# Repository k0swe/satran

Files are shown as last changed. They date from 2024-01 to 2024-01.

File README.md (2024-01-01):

# Open source Azimuth/Elevation satellite antenna rotator for radio amateurs

- Designed by Daniel Nikolajsen, SM7YSA

The onboard microprocessor has wifi-capability and can be controlled
automatically with an easy to use android app that you can install for free from
Google Play, or with the free PC program Gpredict or other rotctld-compatible
software.

The rotator has a mount on top that allows for many different kinds of antennas,
perfect for getting started with satellite communications.

The MK3 Satellite Rotator is fully open source, allowing you to 3D-print the
parts at home for free and solder the PCBs by hand. Enjoy!

If you invent upgrades or find new ways of using the SATRAN, we hope that you
[contact us](https://www.satran.io/support/) and share your designs so we can
post it here on the website for all to enjoy.

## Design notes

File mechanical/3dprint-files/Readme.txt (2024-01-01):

/***********************************************
 2022-11-15
 SATRAN AZ/EL ROTATOR MK3 print files
 ---
 Design SM7YSA Daniel Nikolajsen <satran@danaco.se>
 Creative commons BY-NC-SA 2.0
 www.satran.io
***********************************************/

Gears recommended print settings
---
ASA, ABS or Nylon
0.4mm nozzle
0.15mm layer height
60-70% infill
30-40mm/s print speed
Gears should have a tight fit on to the motor or sensor axle. 
To increase/decrease play, adjust the
infill by 5-10% or resize the entire part by a few percent.

Housing recommended print settings
---
PLA or PETG
0.4mm nozzle
0.2mm layer height
50-60% infill
40-60mm/s print speed
Good luck!

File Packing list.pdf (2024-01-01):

## SATRAN MK3 Rotator – Bill of Materials

2022-09-02

1pcs Controller in plastic casing | 1pcs Rubber grommet PG16
1pcs Power cable | 4pcs Bolt M3x6mm
2pcs DC geared motor 60rpm | 9pcs Countersunk screw 3x10mm
1pcs Bearing 6806 | 14pcs Flange screw 3x8mm
1pcs Bearing F685 | 4pcs Bolt M3x12mm
2pcs Bearing 608 | 4pcs Lock nut M3
1pcs Control patch cable RJ45 | 5pcs Flange nut M8
1pcs Aluminum motor bracket | 2pcs Tapping screw 2.2x10mm
1pcs Aluminum antenna bracket | 7pcs Tapping screw 2.2x6.5mm
1pcs M8 axle with glued lock nut | 7pcs Bolt M5x16mm
1pcs 12volt power adapter | 3pcs Hex nut M5
1pcs 1-turn potentiometer 1kohm | 4pcs Lock nut M5

1pcs 10-turn potentiometer 1kohm

## 3D-printable parts

Official downloads available at www.satran.io/downloads

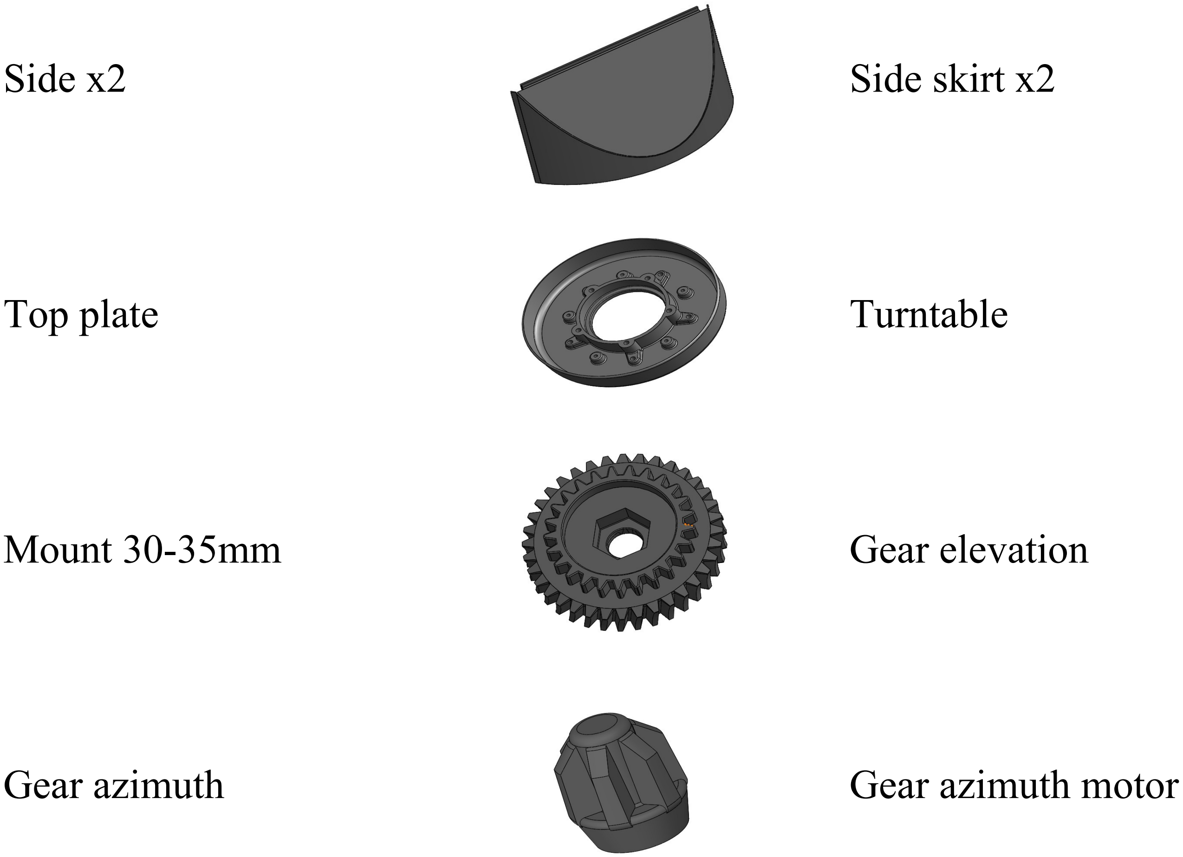
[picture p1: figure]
Side x2; Side skirt x2; Top plate; Turntable; Mount 30-35mm; Gear elevation; Gear azimuth; Gear azimuth motor
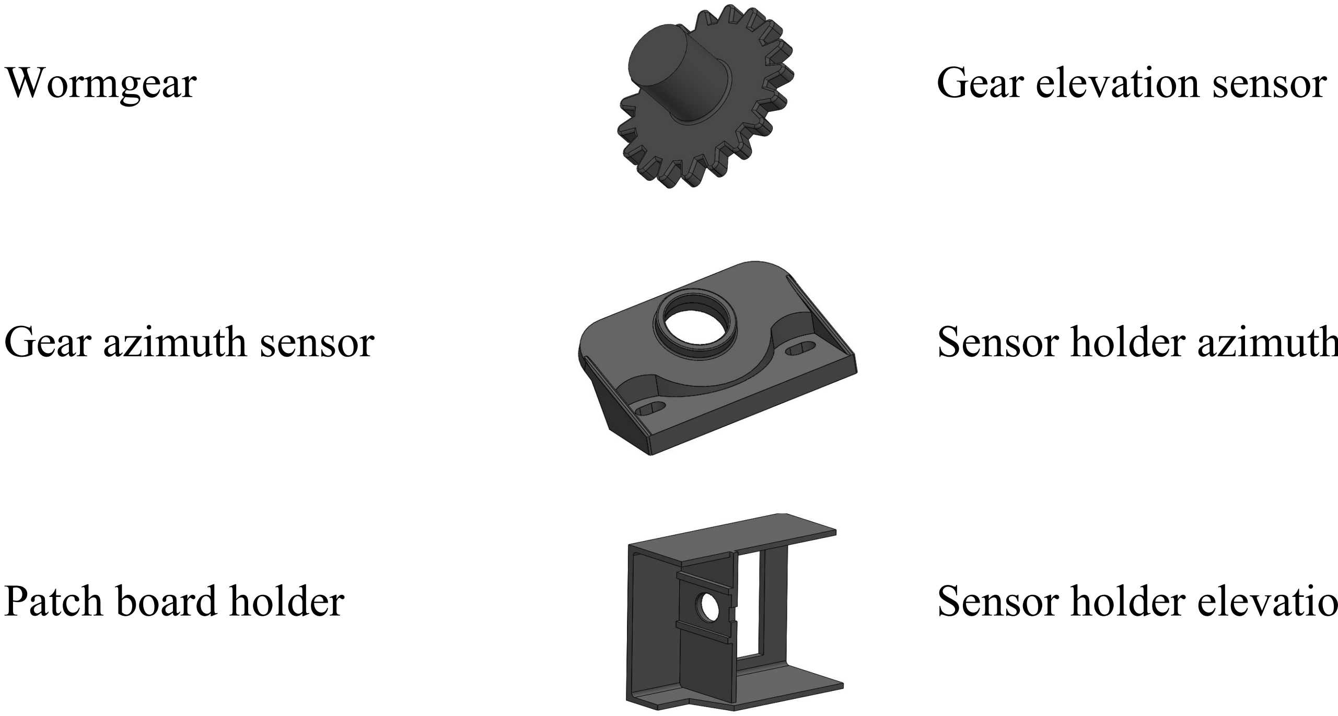
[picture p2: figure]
Wormgear; Gear elevation sensor

Gear azimuth sensor | Sensor holder azimuth

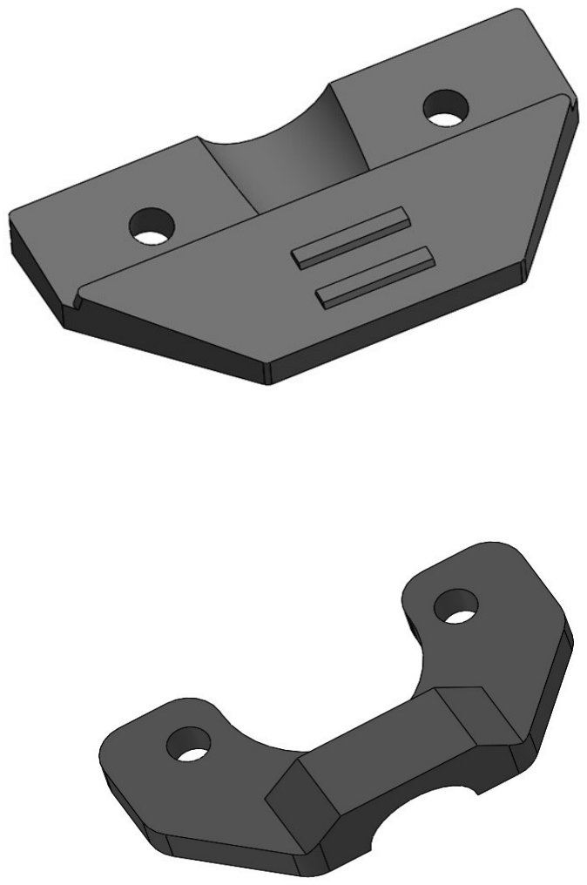
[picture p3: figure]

Patch board holder | Sensor holder elevation
Patch board clamp | Axle spacer

15/20mm antenna fastener

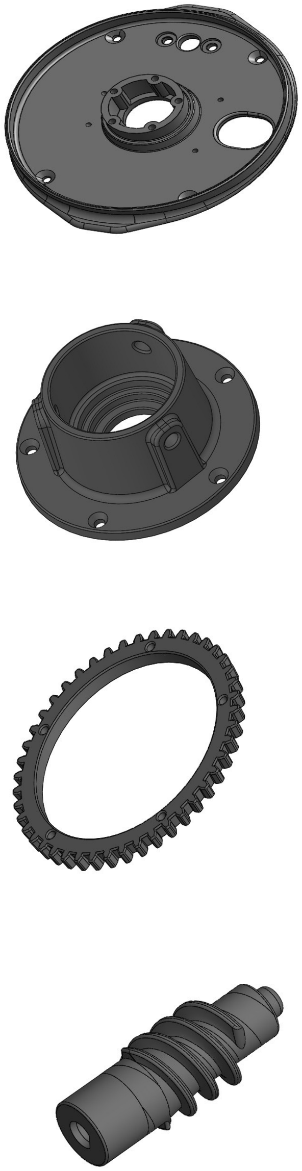
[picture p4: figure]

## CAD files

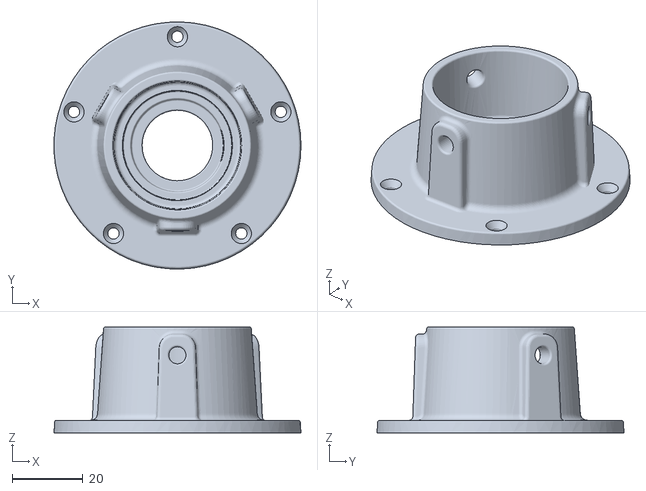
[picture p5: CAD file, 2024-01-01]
mechanical/3dprint-files/pipe-mount.STL
70.0 x 70.0 x 30.0

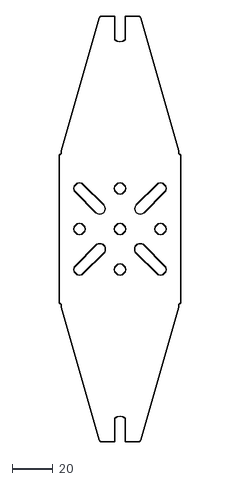
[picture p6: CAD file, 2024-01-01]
mechanical/Antenna bracket flat.dxf
60.0 x 210.0

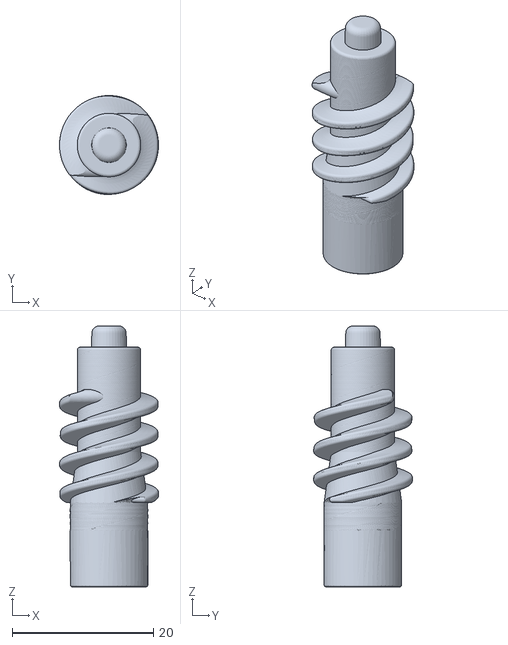
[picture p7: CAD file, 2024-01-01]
mechanical/3dprint-files/elevation-wormgear.STL
14.0 x 14.0 x 37.0

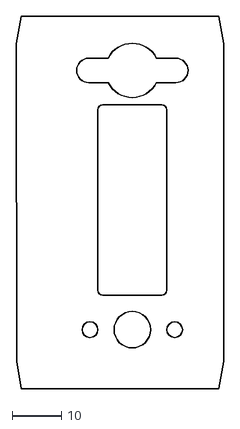
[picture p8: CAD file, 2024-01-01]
mechanical/Elevation motor bracket flat.dxf
42.0 x 75.6

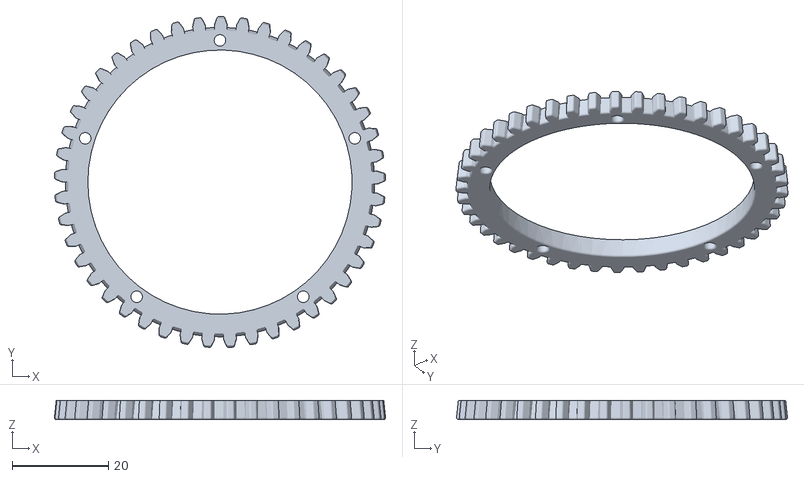
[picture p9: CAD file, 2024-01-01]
mechanical/3dprint-files/azimuth-stationary-gear.STL
68.9 x 68.9 x 4.00

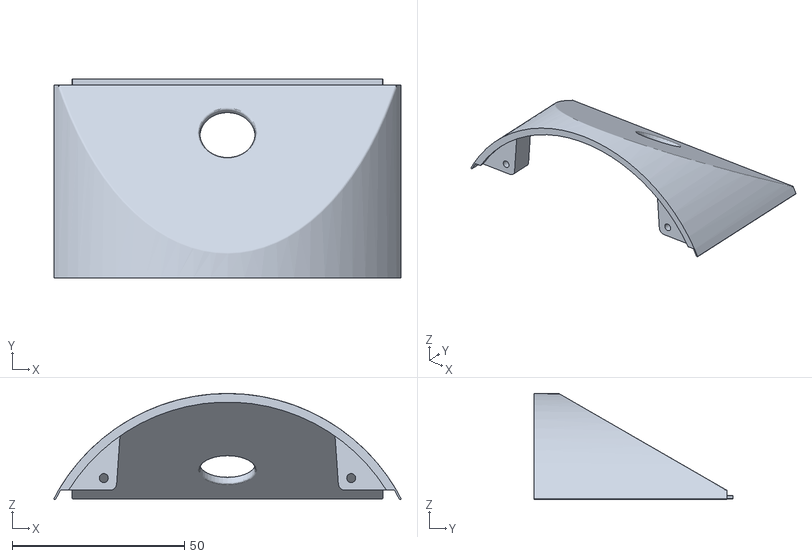
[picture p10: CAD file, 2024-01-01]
mechanical/3dprint-files/side-skirt-grommet.STL
100.8 x 57.8 x 30.8

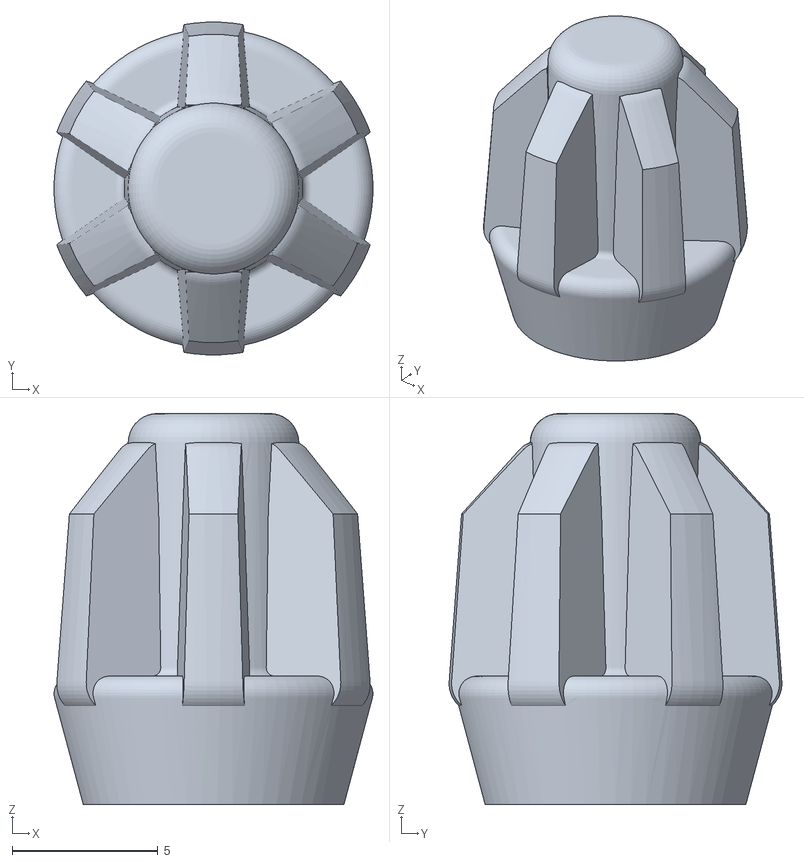
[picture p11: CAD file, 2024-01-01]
mechanical/3dprint-files/azimuth-motor-gear.STL
10.9 x 11.4 x 13.4

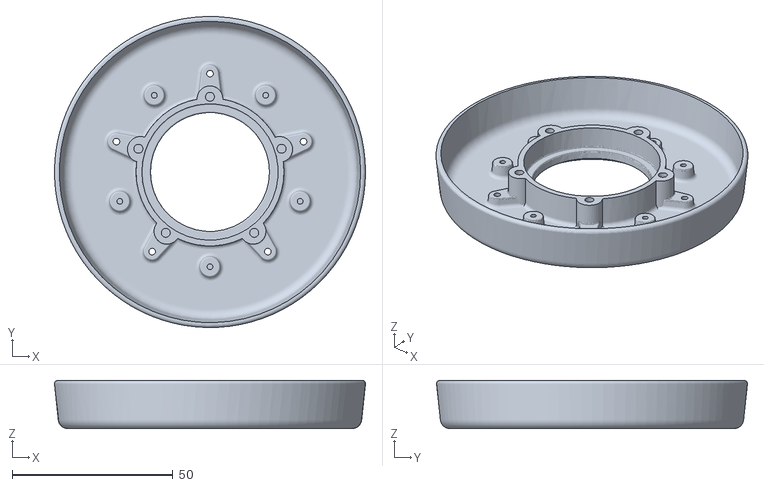
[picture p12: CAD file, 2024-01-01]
mechanical/3dprint-files/turntable.STL
96.8 x 96.8 x 15.0

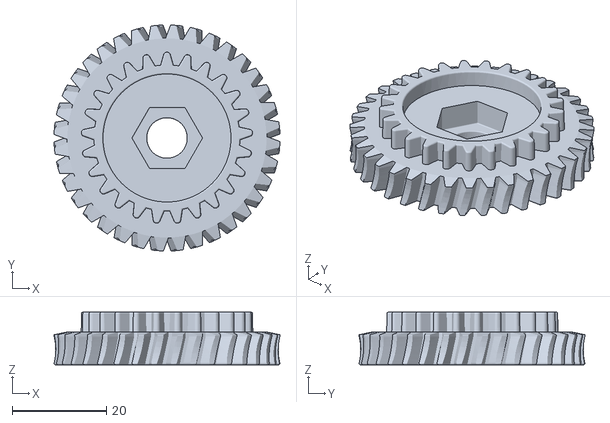
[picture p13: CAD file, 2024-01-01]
mechanical/3dprint-files/elevation-axle-gear.STL
48.0 x 48.0 x 11.2

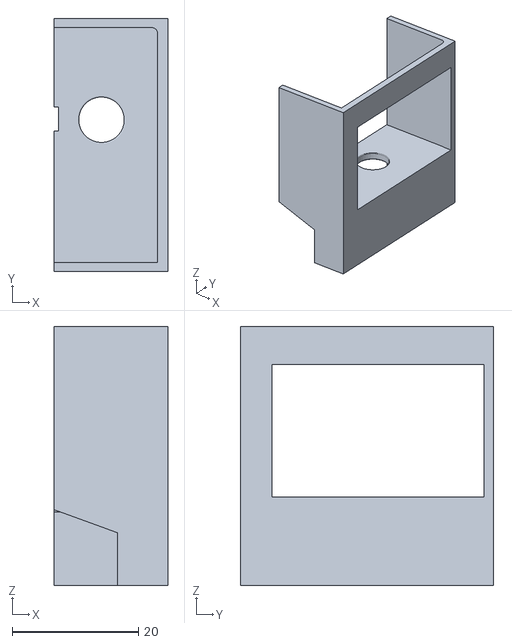
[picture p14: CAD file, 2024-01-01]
mechanical/3dprint-files/elevation-sensor-bracket.STL
18.0 x 40.0 x 41.0

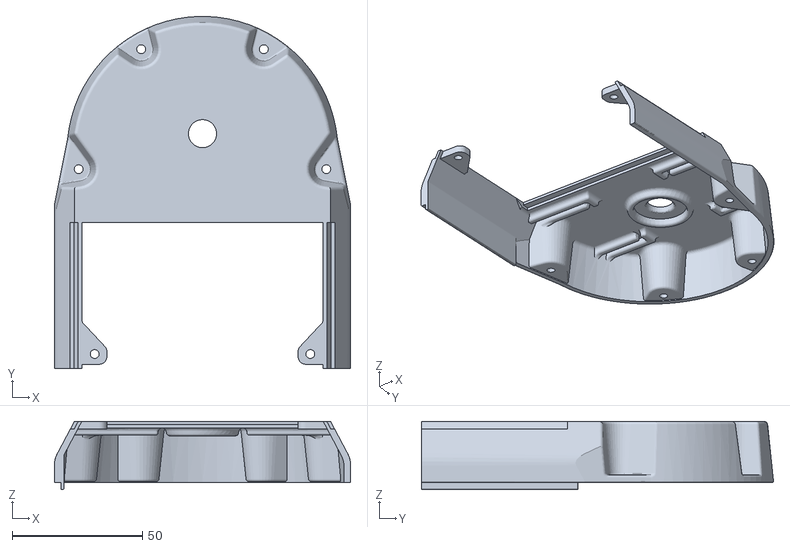
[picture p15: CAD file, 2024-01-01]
mechanical/3dprint-files/side-housing.STL
113.6 x 134.9 x 26.1

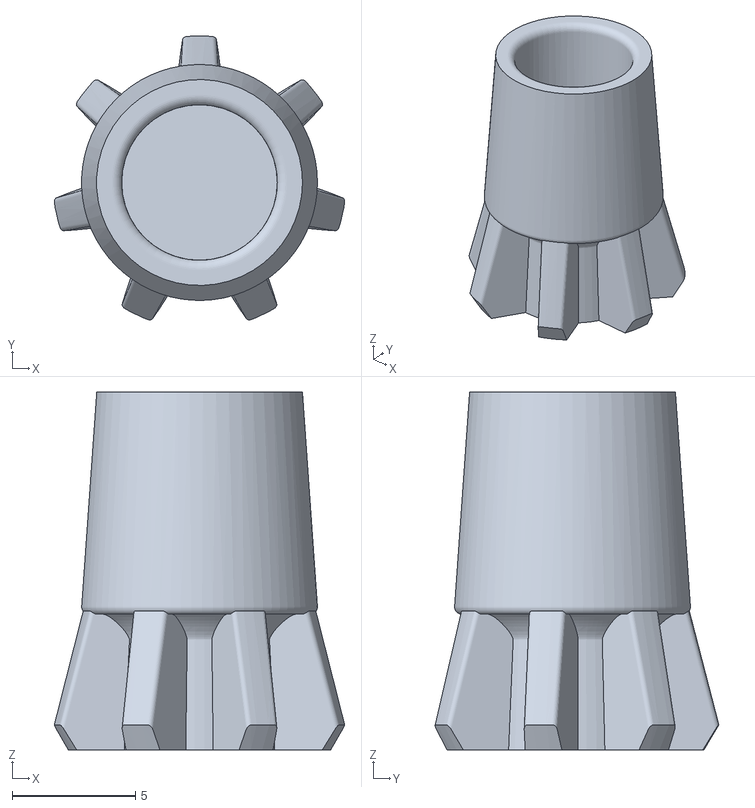
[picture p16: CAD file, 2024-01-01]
mechanical/3dprint-files/azimuth-sensor-gear.STL
11.8 x 11.5 x 14.5

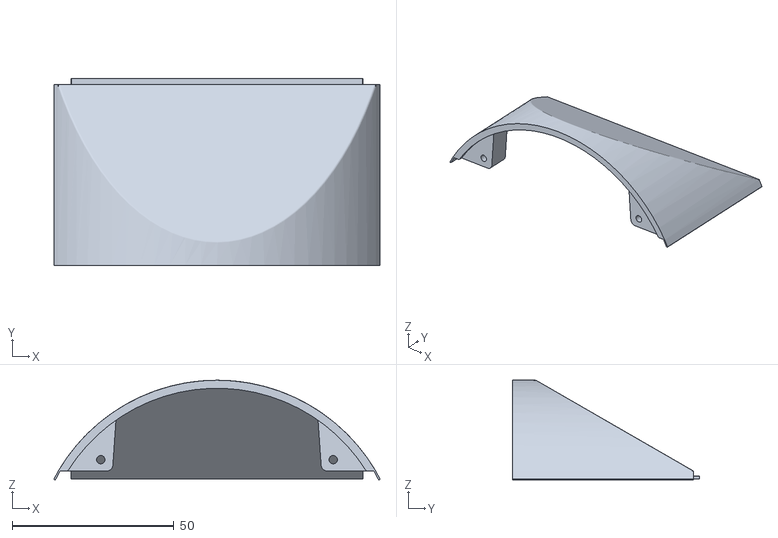
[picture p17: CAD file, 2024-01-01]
mechanical/3dprint-files/side-skirt.STL
100.8 x 57.8 x 30.8

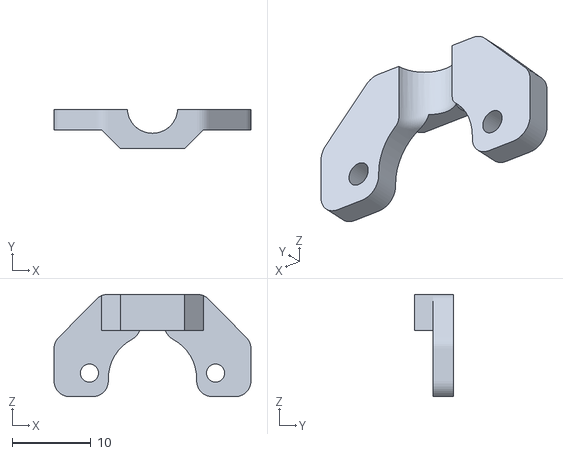
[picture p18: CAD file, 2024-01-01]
mechanical/3dprint-files/patch-board-top-bracket.STL
25.0 x 5.00 x 13.0

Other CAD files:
mechanical/3dprint-files/axle-spacer.STL
mechanical/3dprint-files/antenna-bracket-15mm.STL
mechanical/3dprint-files/antenna-bracket-20mm.STL
mechanical/3dprint-files/azimuth-sensor-bracket.STL
mechanical/3dprint-files/elevation-sensor-gear.STL
mechanical/3dprint-files/patch-board-bottom-bracket.STL
mechanical/3dprint-files/top-plate.STL

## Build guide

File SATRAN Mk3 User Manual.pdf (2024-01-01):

# SATRAN

# MK3 USER MANUAL

SAtellite TRacking ANtenna

Experimental 3D-printable azimuth/elevation antenna rotator

www.satran.io

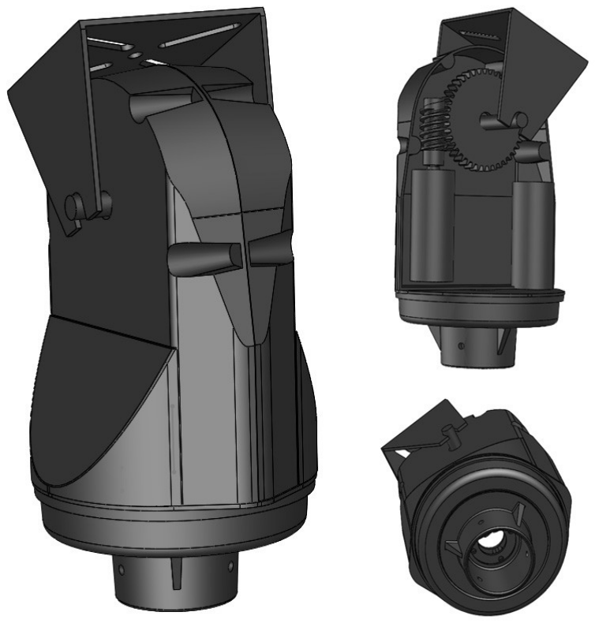
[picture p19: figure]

Within Europe only legal for use by authorities or licensed radio amateurs

Always read and understand this manual before use

2022-10-09 | page 1

## Safety Precautions and Instructions

Before use, read all parts of this manual to prevent injury or malfunction

1) Inspect the product after unboxing and do not continue with the installation in case there are parts missing or the product has any visible damage.
2) The control unit needs a stable DC 12V 1A power supply to function properly, you are advised to only use the supplied power adapter or it may result in damage to the unit.
3) Ensure that the operating environment meets the specifications stated in this data sheet.
4) Do not store or mount any electrical parts of the product in such manner that they can be exposed to water or other chemicals. The rotator housing is splash-proof but prolonged exposure to liquids might damage it.
5) Protect the product from sources of high voltage, lightning or electromagnetic interference. The unit has some protection for EMI, but high antenna transmitting powers might affect the functionality or even damage the control unit.
6) When installing or using the product, make sure that the rotator and any externally mounted antenna have enough space to move freely without hitting something or someone before you connect any power cables.
7) Never use the product if it is damaged in any way or operating unexpectedly.
8) Never use the product if you do not have sufficient knowledge or licenses. It is the responsibility of the operator to follow local laws and regulations, and to maintain the proper permissions.
9) Should any abnormal odour, noise, smoke, temperature rise or vibration be detected; stop using the product immediately, remove power and any connected communication cables.
10) Do not operate in strong winds which may cause antennas, rotator or parts of it to get damaged or come loose and hurt people or property.

## Getting started

Visit www.satran.io for the latest instructions on how to 3D-print and assemble the unit.

The default mount is intended for a 35mm pipe, preferably a PA speaker stand with any plastic center plugs removed for the cables to run through the center.

Warning! Before connecting power to the device, make sure it has enough room to move freely without hitting something. When power is applied, the rotator will initiate by moving both axis.

1) Mount the Satran on top of a pipe with control cables and any coaxial cables running inside down through the pipe, without fastening it completely.
2) Mount the control unit below the rotator, approx 1 meter away from the device or any other sources of electromagnetic interference. Cables coming in or out of the plastic housing should do so in the bottom to prevent any rainwater entering. Connect the control cable from the Satran to the RJ45 port on the controller, and the 12V power connector to the JST-plug on the controller.
3) Connect the power cable to a recommended power adapter and wait a few seconds for the rotator to initialize. If all is well, it should move both the azimuth and the elevation for some distance.
4) Start your computer or smartphone and connect it to the wireless hotspot with a hostname starting with ”SATRAN_”
5) Open a browser window and enter http://192.168.4.1/calibration and perform the steps stated in this manual on page 5 to calibrate the sensors. Restart the device when finished.
6) After initialization, the rotator points to what should be 0 degrees north (you can check the direction by visiting http://192.168.4.1). Take a compass and place it on top of the antenna. Turn the rotator by the pipe mount until the antenna is facing geographic north and fasten it by tightening the bolt on the pipe mount.
7) Now you can control the rotator. No more steps are needed if you only want to control the rotator directly. Enter http://192.168.4.1 in a web browser to access the manual control interface or enter the IP in the settings of your desired software like ”Satran Control” android app or Gpredict on PC. Note! Using an SSL-prefix https:// does not work and will only give you an error page.

Continue if you want to control the Satran over your wireless network (recommended)...

8) Open a web browser and enter http://192.168.4.1/setup
9) Choose your desired wireless network from the list and enter the required password, press to save. Satran now restarts.
10) Now you can connect the computer or smartphone back to your own WLAN and the Satran can be accessed by replacing the IP-address with the one assigned to it by your wireless router. If you do not know this, you need to login to your wireless router and check what IP-address it has been assigned by the DHCP service. If the Satran is unable to connect, you might need to reset it to factory defaults and try again.

## Mounting the device and antenna

It is important that both the Satran and any antennas are mounted properly to minimize the risk of damage to the unit or its surroundings.

The rotator should always be mounted facing upwards to prevent rain or dust entering it.

Satran is intended for all cables running through the center of it down the mounting pipe. On the side of the rotator there is a rubber gasket for the antennas coaxial cable. If the tubing that your Satran is mounted on is taller than the control cable, you will need to drill a hole in the pipe approx 1 meter below the top where the cable can exit for connection with the control box.

The DC power jack on the power cable is not waterproof and should be protected or sealed from the elements if it may be exposed to rain or moisture.

The control box should be securely mounted with the cables coming out from the bottom, using a rubber gasket for the cables and the silicone-sealed lid fastened. The built-in antenna on the controller is slightly directional and the control unit should always be mounted vertical to maximize wifi range. Do not mount the controller in a metal housing that will shield the wifi-signals.

A maximum antenna weight of 500 grams is recommended even if the motors are strong enough to handle weights of up to 1kg. The plastic gears are often the weakest link, and with a heavy antenna it is of extra importance to use lubrication on the wormgear (elevation). The antenna should be balanced with a slight overweight in the front of the Satran when in a horizontal position.

Satran does not know what is north or south. When you mount the rotator, connect power to it and let it finish initialization. Then put a compass along the top bracket or antenna and manually turn the entire rotator until the ”front” is facing 0 degrees north. Now tightly fasten the screws on the rotator mount. Remove and reconnect power again and make sure that sensors has been read correctly and that it is still facing north, otherwise redo the procedure and adjust.

Use plastic wire straps to fasten any cables to prevent strain on the connectors and other damage that could be caused by wind or gravity.

## Reset to wifi defaults

If you need to reset the wifi settings and start the default Access Point again, you need to reset the controller to factory defaults. Do this by pressing and holding the reset-button on the top left of the controller board for a minimum of 3 seconds until a bright LED-light turns on. Release the button and wait 10 seconds for the Satran to restart. This does not affect sensor calibrations.

## Powering up or down

To turn off the Satran; just disconnect the power. There are not any manual boot sequences or commands. When you reconnect power again it will boot up in a clean state but will remember any saved wifi credentials or calibrations.

It is recommended to always disconnect power when the device is not in active use.

## Calibration of sensors

The Satran MK2 uses two linear 1K potentiometers as sensors to read its current position. The max/min values of these need to be calibrated in order to give a high accuracy. The rotator accepts potentiometer range of 25 - 999. A reading lower than approximately 25 probably indicates that the control board has lost connection with the sensor; in that case check your cables.

1) Mount the rotator correctly and
power it up. Wait a few seconds for
the device to initialize.

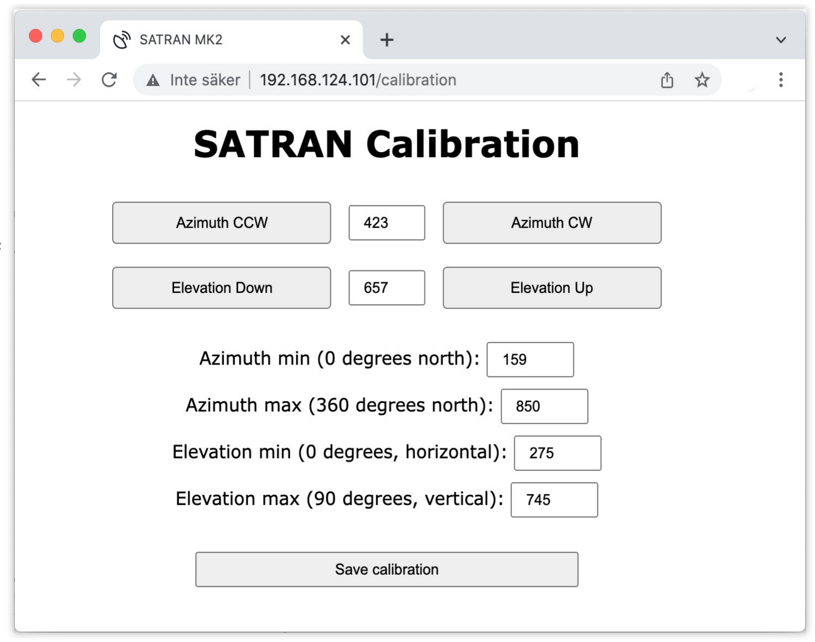
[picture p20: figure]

2) If the device has not yet been setup and connected to you WLAN, connect your computer or smartphone directly to the Satran Access Point (hostname starting with
”SATRAN_”).
3) When connected, open a web browser window and enter
http://192.168.4.1/calibration into the URL field if accessing it directly on the access point, or replace the IP-address with the one assigned to it
by your wireless router.
4) Click to turn the azimuth counter-clockwise until it reads approx 150-200. This number will be the north end position (0 degrees). Enter this value in the corresponding field and press save button.
5) Take a pen or piece of tape and make a marking on both the bottom fixed turntable and the top rotator housing that should line up with each other.
6) Press the ”Azimuth CW” button repeatedly to turn the azimuth a full 360-degree turn until the markings you made lines up again. Enter this new azimuth reading into the corresponding ”azimuth max”-field and press save. Approx 900 is the maximum of the sensor, and when moving closer to this value you might get irregular readings, which indicates that the sensor has moved too far. Remove the markings/tape on the rotator when finished.
7) Continue by slowly and repeatedly pressing ”Elevation down” button until the top antenna bracket is horizontal (0 degrees) Enter the elevation reading into the corresponding ”Elevation min”-field and save.
8) Press ”Elevation up” until the antenna bracket is vertical (90 degrees) and enter the reading as the ”elevation maximum”, press to save settings.

Now calibration is finished. Restart the device and continue with the wifi setup.

## Controlling manually via browser interface

When installing or testing the Satran, it is good to have a way of controlling it without needing any additional software. That's why it has a manual control that you can access directly from any standard internet browser.

If setup has been performed and Satran is connected to your WLAN, enter:

http://192.168.x.x (http://192.168.x.x/control) (change IP-address to the one it has been assigned by your WLAN)

If you are accessing the Satran directly, via the built-in access point (SSID: SATRAN_***):

http://192.168.4.1 (http://192.168.4.1/control)

## Control with the Android app

The easiest way to use the Satran is with the free android app ”Satran Control” available for download from Google Play.

After installation, start the app and go to the settings tab. Enter your GPS location and the correct IP-address to the Satran. If setup has been performed, use the IP that it has been assigned to it dynamically by your wireless router. If you are accessing the Satran access-point directly, the given IP-address is always 192.168.4.1

Now click the tab for the satellite list and choose any by clicking on it. If the list is empty, you need to connect your android device to a WLAN with internet access and restart the app to fetch a new satellite list from the CelesTrak data server.

When a satellite has been chosen, you can go to the first tab that should show you its relative position and the time for its next overhead pass. If you want the Satran to track the satellite when it passes you, you need to click the toggle button on the prediction tab to activate the rotator.

Please mind that the app will keep sending commands to the Satran even when minimized in the background. For the Satran to stop you need to deactivate it by pressing the toggle button in the app, or completely terminate the app.

## Control with HTTP GET request

The app uses very simple GET requests to control the Satran, which are sent as a readable URL over HTTP on port 80 that you can test manually with any web browser: Http://192.168.x.x/tracker?az=123&el=123

The IP-address above (192.168.x.x) should be replaced with the one it has been assigned by your wireless router. Replace ”123” with the direction you want in degrees 0-360 for azimuth and 0-90 for elevation. Wait a second and the rotator should move and the browser sends back the string ”success”.

## Control with Gpredict (hamlib/rotctld)

The Satran has a simulated hamlib rotctl daemon or ”rotctld” that acts as a TCP server and can take standard rotctl commands from compatible software, like the popular Gpredict program.

When power is connected and the rotator has initialized without errors the Satran is always listening for rotctl commands, which makes setup very easy.

1) Power up the Satran and connect the computer with Gpredict either directly to the access point or the wireless network that the Satran is connected to.
2) In Gpredict, click ”edit” and ”preferences” in the top bar

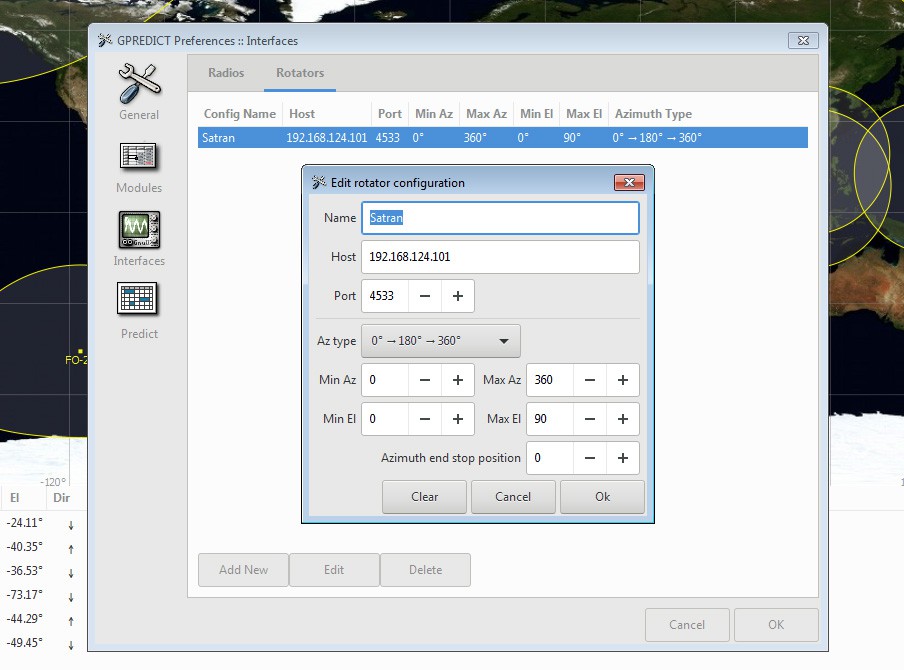
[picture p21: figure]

3) Press ”interfaces” in the left column and choose the tab ”rotators”. Press ”Add New”. Enter the IP-address to the Satran and the other settings as pictured above. Press OK to close all.
4) In the main Gpredict window, now click on the small arrow icon in the top right corner to bring up the menu containing ”Antenna Control”. Click on it.

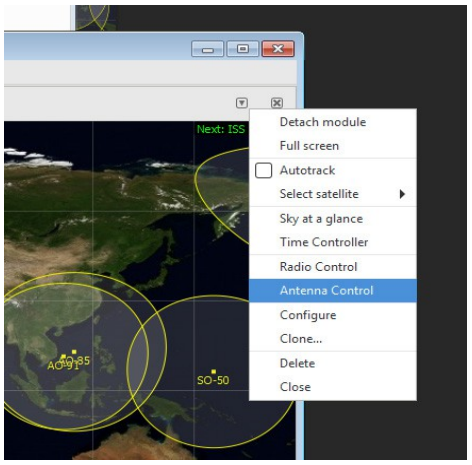
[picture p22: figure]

5) First press the ”engage”-button to connect with the rotator. Next choose the desired satellite from the dropdown under ”Target” and click the button ”Track” to automatically follow the satellite when it reaches AOS (enters over the horizon). You can also manually change the large numbers for azimuth or elevation and the rotator will turn accordingly.

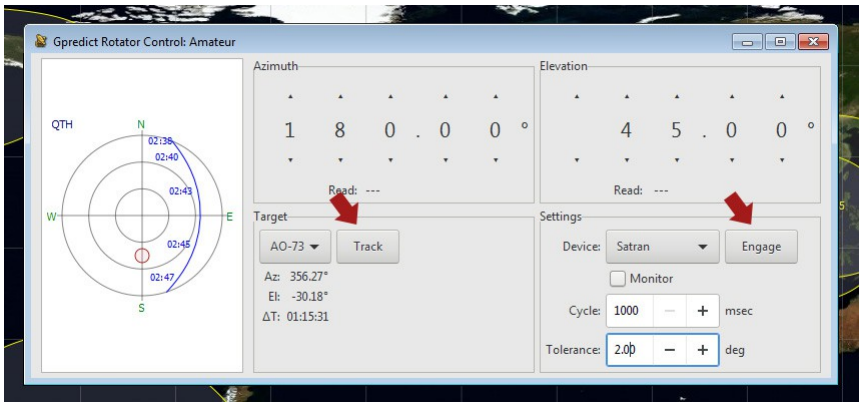
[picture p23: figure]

Satran MK2 has not yet been tested with other hamlib/rotctl-compatible software like satnogs. If you get it to work with such other software, please be kind to the community and share your findings in the forum at www.satran.io or by mail to satran@danaco.se

## Specifications MK3

Control unit processor: | ESP8266 v2 NodeMCU
Recommended PSU: | DC12V 1A
Control unit power cable: | JST-XH 2pin to 5x2.5mm DC-plug
Voltage requirements: | DC 11-14 volt
Recommended fuse: | 5x20mm 630mA
Motor rated voltage: | DC12V 60RPM
Wifi network compatibility: 802.11 b/g/n (max 20 character pass/ssid)
Azimuth movement: | 0-360 degrees
Elevation movement: | 0-90 degrees
Tolerance: | approx 5 degrees
Operating temperature: | 0 to +30° Celsius
Max antenna weight: | 500 gram recommended
Weight, finished unit: | approx 500gram
Dimensions rotator: | 200x120x120mm
Dimensions control box: | 110x110x70mm
Standard pipe mount: | 25mm-35mm
Country of origin: | Sweden

### Happy satellite hunting!

### 73 de SM7YSA Daniel Nikolajsen www.satran.io

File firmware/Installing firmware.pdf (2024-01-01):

2022-10-09 | www.satran.io

# Updating the Satran MK2/MK3 Firmware

1) First download the latest binary firmware from https://www.satran.io/downloads and then install the official ”Espressif Flash Download Tools” for Windows PC:
https://www.espressif.com/en/support/download/other-tools?keys=&field_type_tid%5B%5D=14
2) Unpack the compressed program files to a new folder
3) Right click the exe-file and choose to ”Run as administrator”

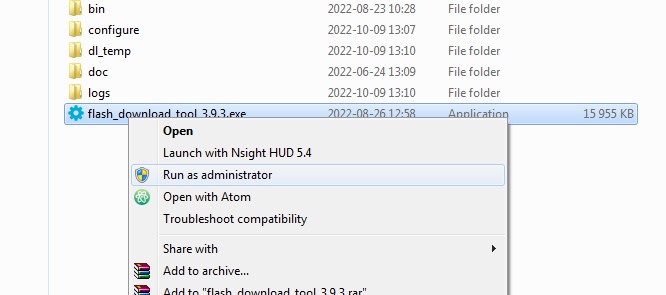
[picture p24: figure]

The program opens a black terminal screen in the background that you should leave open

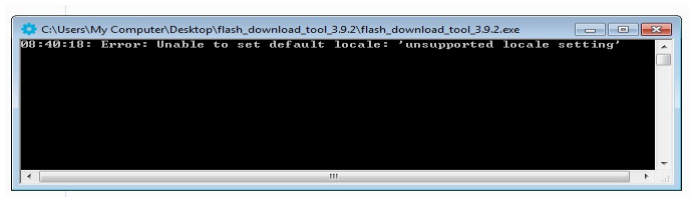
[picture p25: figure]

4) Choose default ChipType ”ESP8266” and WorkMode ”Develop”, press OK

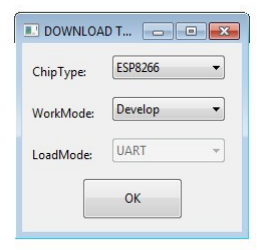
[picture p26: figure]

2022-10-09 | www.satran.io
5) Remove all cables connected to the board (power or rotator connector) and connect a
micro-USB cable (”smartphone charging cable”) between the computer and the Satran controller.

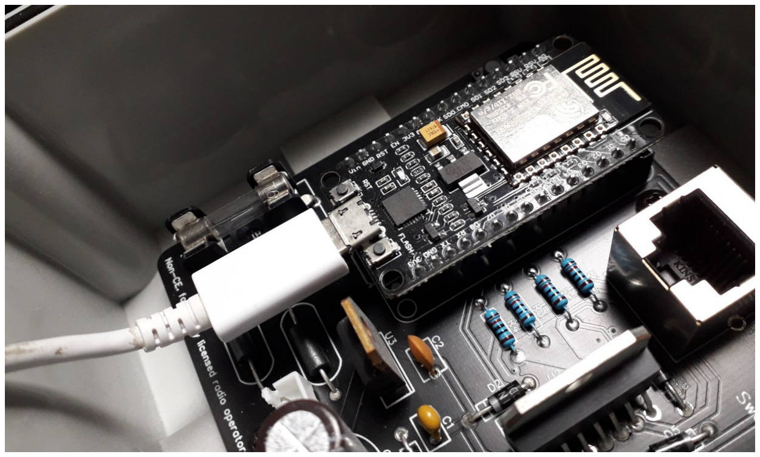
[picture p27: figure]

6) In Espressif Download Tools, press the top button with three dots to browse for the Satran precompiled binary firmware file that you downloaded earlier

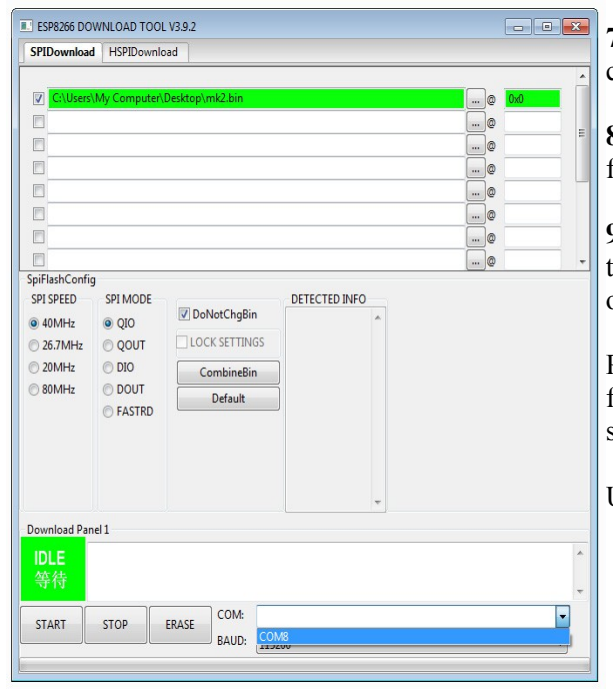
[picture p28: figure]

7) Enter the hex target address for the controller which is ”0x0”
8) Mark the checkbox left to the binary filepath, to include it in the upload
9) Choose port in the ”COM” dropdown. When the USB is connected, it should only have one option that you can pick.

Press the ”START” button and wait until finished. The LED on the control board will start to flash until the upload is finished.

Unplug the USB-cable and close the program.

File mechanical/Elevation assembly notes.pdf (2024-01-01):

### Assembly of Satran MK2 elevation

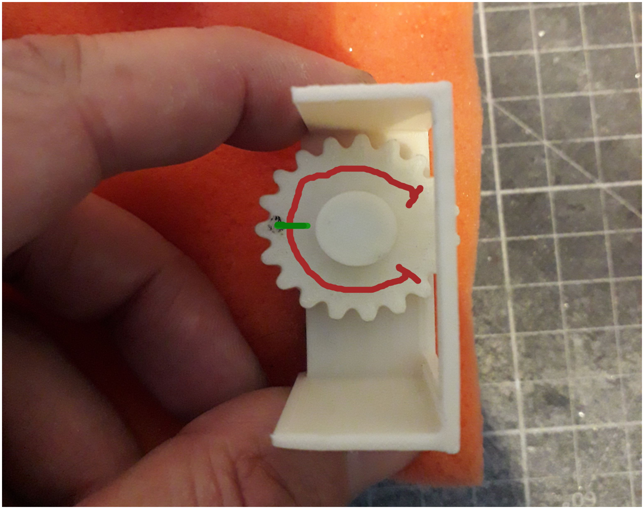
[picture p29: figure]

Rotate the elevation sensor to its center position, make a marking with a pen to help keep it correctly adjusted on assembly.

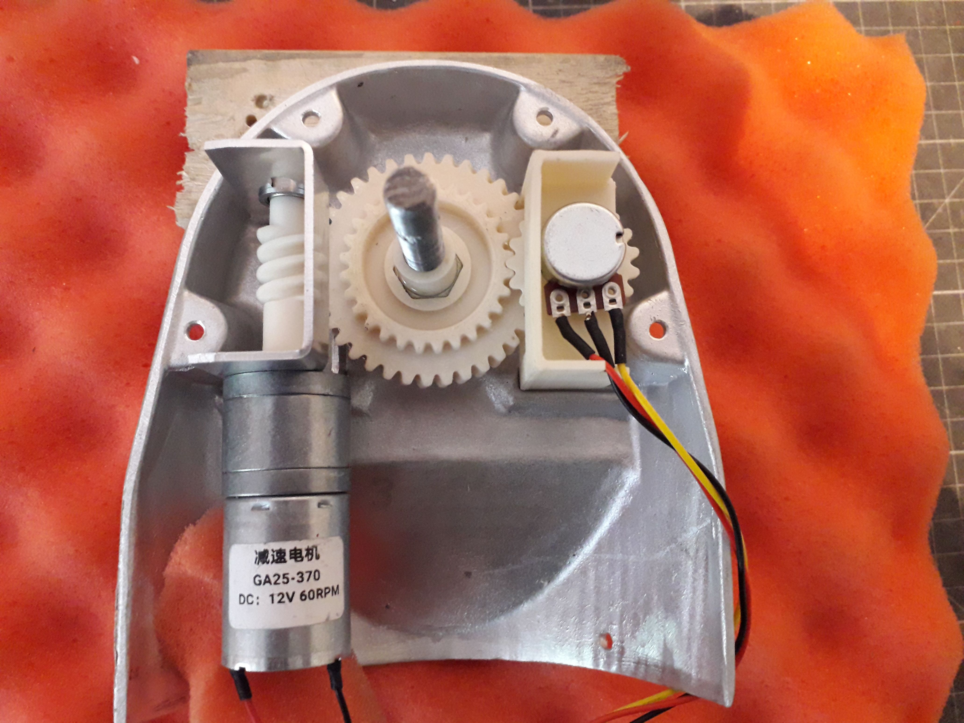
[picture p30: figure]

Add motor, axle and sensor like in the photo to the first enclosure side (the one without the rubber cable grommet).

If needed, put a small amount of silicone along the edge of the side.

The slits on the main axle for the antenna bracket should be in a 45 degree angle towards the motor as in the photo, which is the center position for the elevation axle.

Add the bearing and second side housing, stand everything upright on a flat surface and fasten together with screws. A friendly assistant or a rubber band can help keep the two sides together while fastening.
Wipe off any excess silicone.

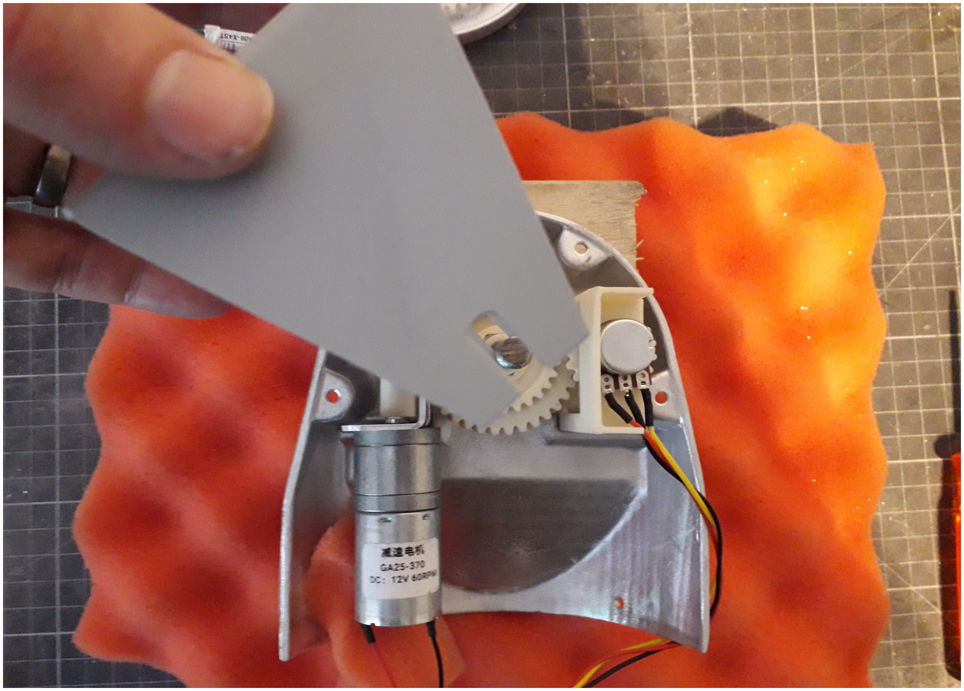
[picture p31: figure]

www.satran.io | 2022-07-02

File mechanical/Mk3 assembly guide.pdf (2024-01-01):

## MK3ASSEMBLYINSTRUCTIONS

2022-08-30 | www.satran.io

1

4 | 5 | 6

9

Unpackthekitandmake
sureallpartsarepresent

Fasten3pcsM5boltsand
hexnutstothepipemount

Fastenthelargeazimuth
gear(short2.2mmscrews)
andthebearingtothe
turntable(3x10mmscrews)

Jointhe10-turnazimuth
potentiometerwithaholder
andaddageartotheaxle

Fastenthesideskirtstothe
sideswith3x10mmscrews

Jointheelevationmotor
withabearing,gearand
bracket(M3x6mmbolts)

Fastenamotor,control
cableandazimuthsensorto
thetopplate

Jointhesmallelevationpot
withaholderandgear

Fastenelevationgearonto
theaxlewithanM8nut
(optionallyaddloctite/glue)

7 8

2 3

10

13 | 14 | 15

18

Addthesmallgeartothe
azimuthmotoraxle.

Layonesideonatableand
putabearingintheslot.

Turntheelevationsensorto
itsmiddleposition(goodto
markitwithapen).

Makesuretheslotsonthe
axlearepointing45degrees
aspictured.

Addmotor,axle,sensor,
spacerandbearingtothe
side.

Addtheremainingsideand
fastentogetherwithM3
boltsandnuts.

Fastentheelevationtothe
topplatewith4pcs
countersunkscrews.

Connecttheelevation
cablestothepatchboard.

Addtwoøangenutson
eachsideoftheaxle.

16 17

11 12

19

22 23

Slidetheturntableonthe
topplateandfastenwith
5pcs3x10mmscrews.

Nowfastenthepipemount
tothebottomwith5pcs
countersunkscrews.

Putthedeviceontopofa
tripodwithcablerunning
throughmiddle.Fasten.

Mountthecontrolboxand
cables,butdon’tconnect
poweruntilsetup.

Addbracketwithantenna
andfastenevenly,notto
breakthegearsinside.

20 21

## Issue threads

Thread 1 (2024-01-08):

GPIO 16 isn't appropriate for RESET button

xylo04, 2024-01-08:
In the current board layout, the WiFi reset button is connected to the NodeMCU GPIO 16 on one side, and through a 10k ohm resistor on the other. The ESP8266 [supports](https://arduino-esp8266.readthedocs.io/en/2.5.2/reference.html#digital-io) a digital pin mode called `INPUT_PULLUP` on GPIOs 0-15, and `INPUT_PULLDOWN_16` on GPIO 16. The circuit as-is causes GPIO 16 to float and always register `LOW` after the button is pressed.

xylo04, 2024-01-08:
We've pretty much used up the available GPIOs on the ESP8266. Maybe we can still use GPIO 16 but change R5 from a pull-down to a pull-up? Then we can use the `INPUT_PULLDOWN_16` mode.

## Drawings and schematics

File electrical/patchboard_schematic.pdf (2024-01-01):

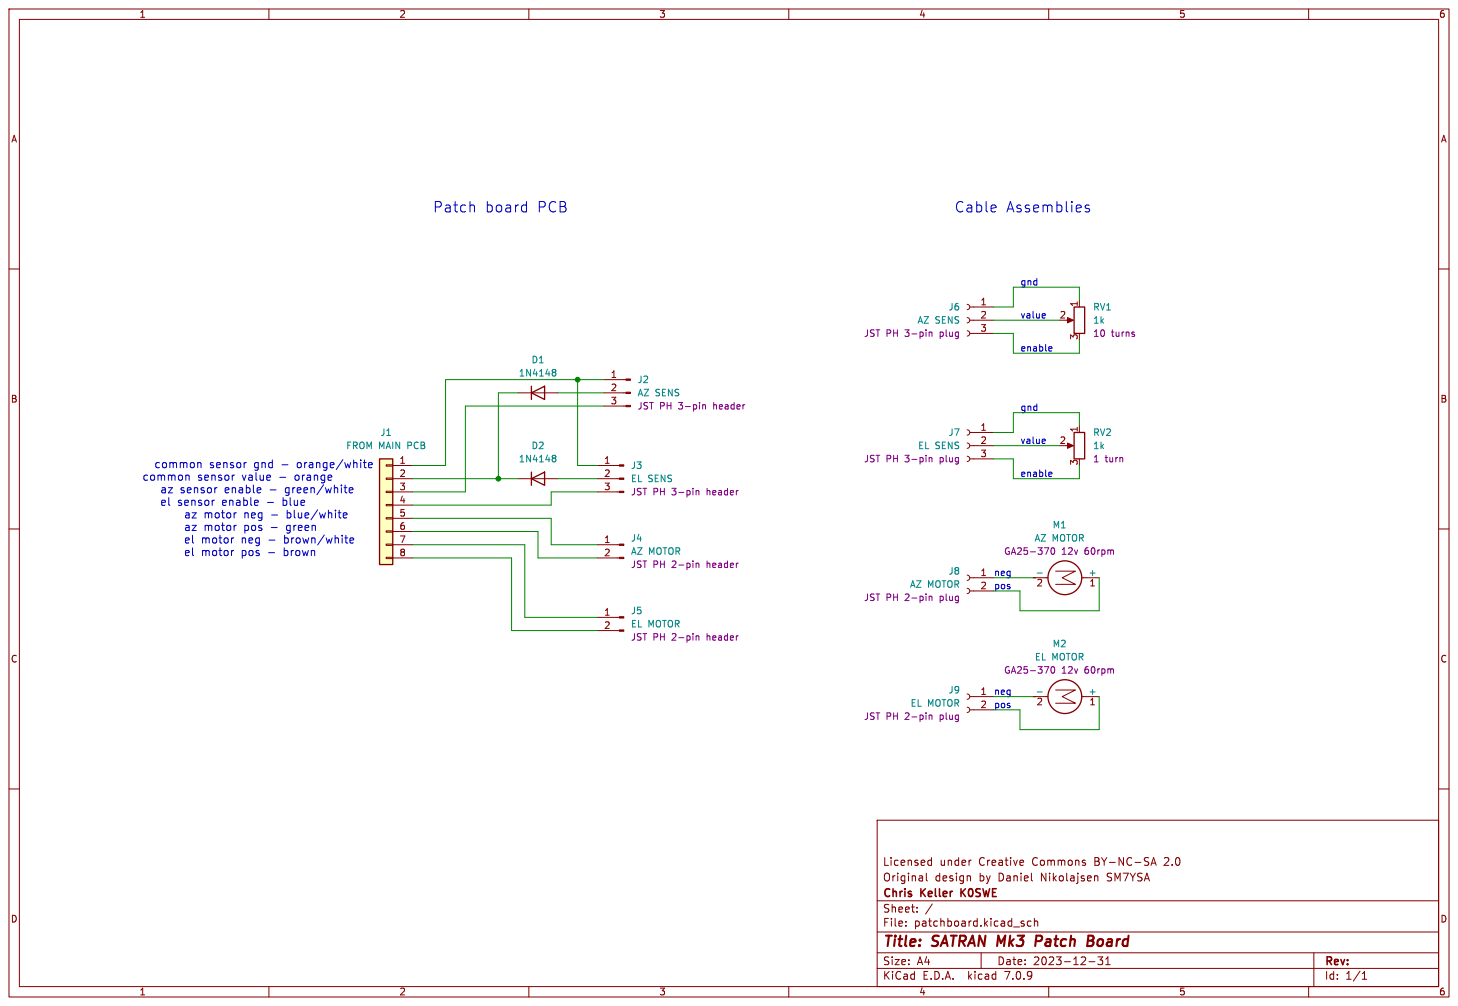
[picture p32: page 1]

common sensor value - orange
az sensor enable - green/white
el sensor enable - blue
az motor neg - blue/white
az motor pos - green
el motor neg - brown/white
el motor pos - brown

Id: 1/1 Title: SATRAN Mk3 Patch Board

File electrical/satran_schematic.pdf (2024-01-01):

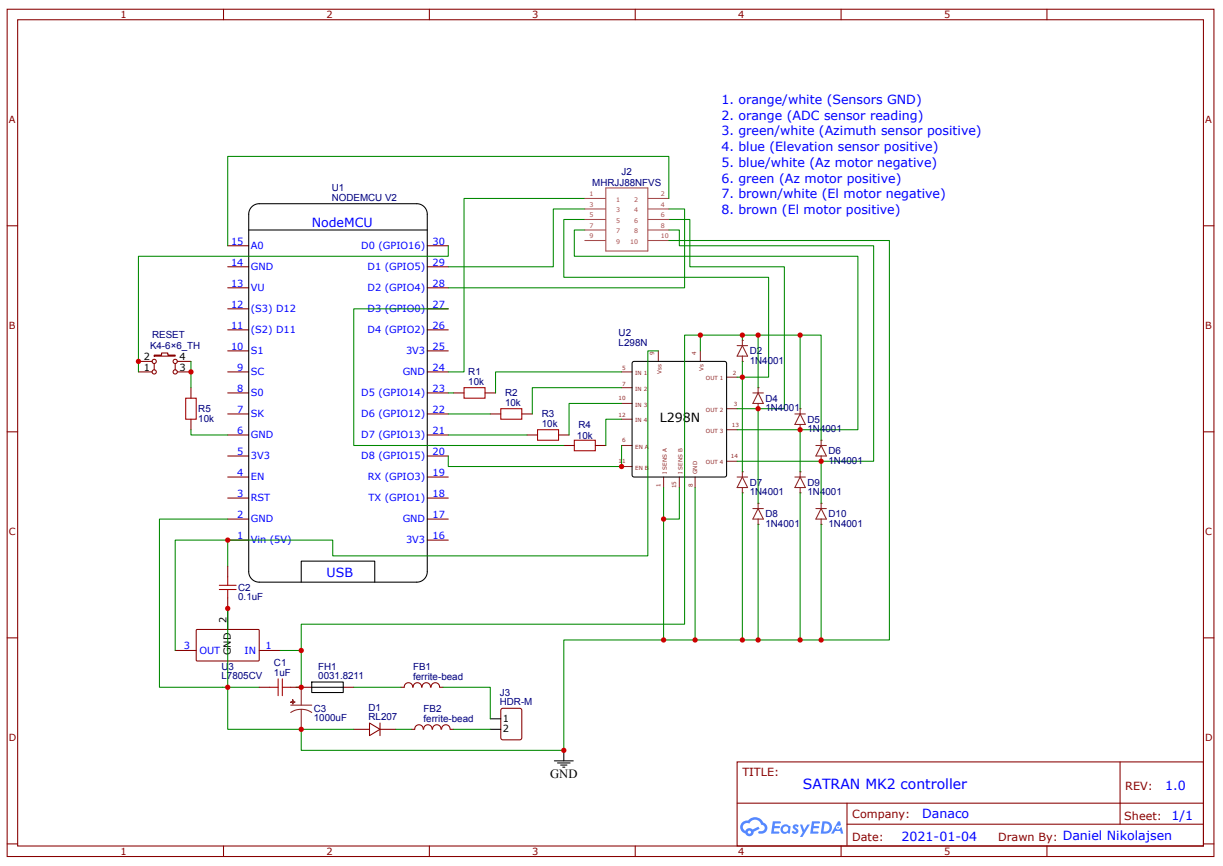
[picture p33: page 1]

1. RUDQJH/ZKLWH (SHQVRUV GND)
2. RUDQJH (ADC VHQVRU UHDGLQJ)
3. JUHHQ/ZKLWH (A]LPXWK VHQVRU SRVLWLYH)
4. EOXH (EOHYDWLRQ VHQVRU SRVLWLYH)
5. EOXH/ZKLWH (A] PRWRU QHJDWLYH)
6. JUHHQ (A] PRWRU SRVLWLYH)
7. EURZQ/ZKLWH (EO PRWRU QHJDWLYH)
8. EURZQ (EO PRWRU SRVLWLYH)

7I7LE: SA7RAN MK2 FRQWUROOHU | RE9: 1.0

CRPSDQ\: DDQDFR | SKHHW: 1/1

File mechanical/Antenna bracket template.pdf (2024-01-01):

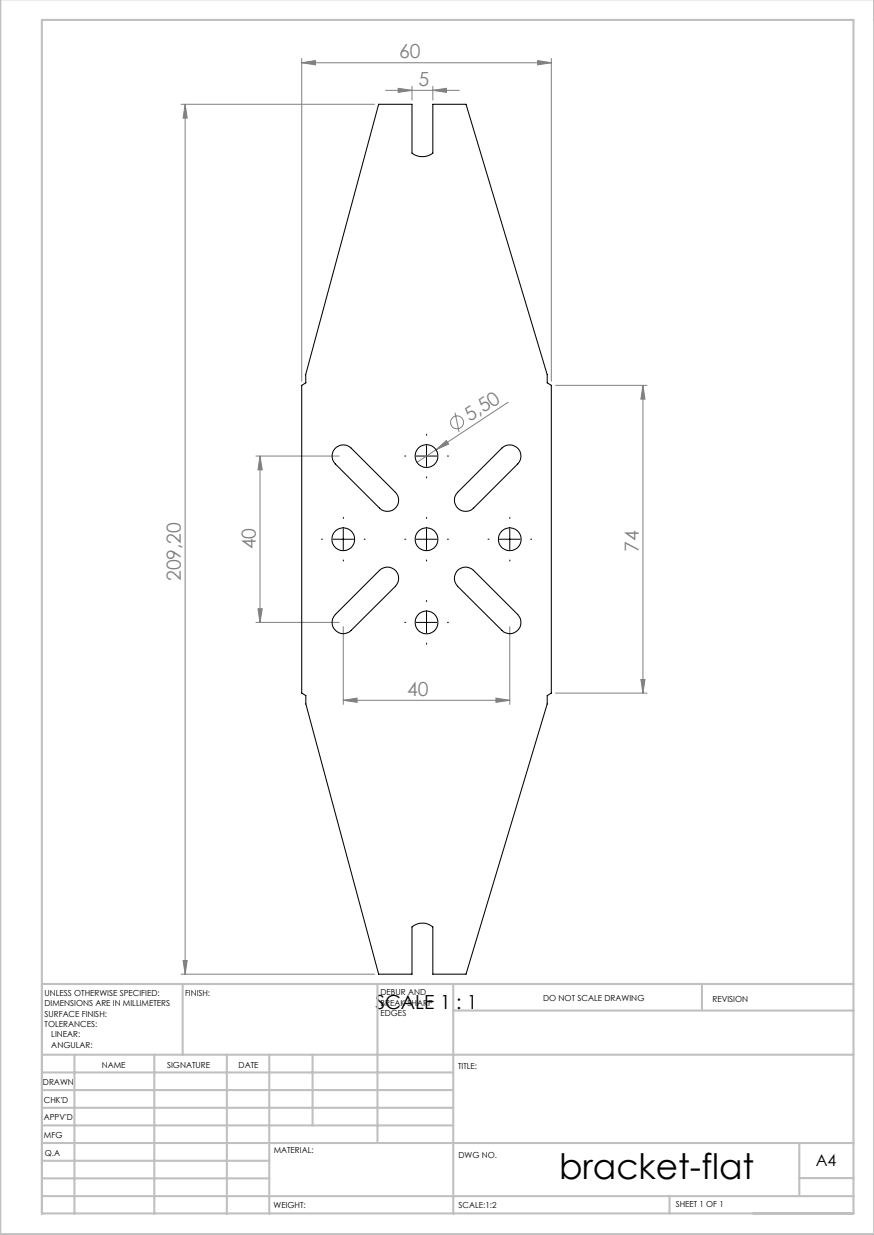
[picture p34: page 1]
SCALE 1 : 1; SCALE:1:2; SHEET 1 OF 1; DO NOT SCALE DRAWING; REVISION; DEBUR AND BREAK SHARP; UNLESS OTHERWISE SPECIFIED:; FINISH:

DIMENSIONS ARE IN MILLIMETERS
SURFACE FINISH:
TOLERANCES:
LINEAR:
ANGULAR:

NAME | SIGNATURE | DATE | | | | TITLE:
Q.A | | | | MATERIAL: | bracket-flat WEIGHT: DWG NO. | A4

DRAWN
CHK'D
APPV'D
MFG

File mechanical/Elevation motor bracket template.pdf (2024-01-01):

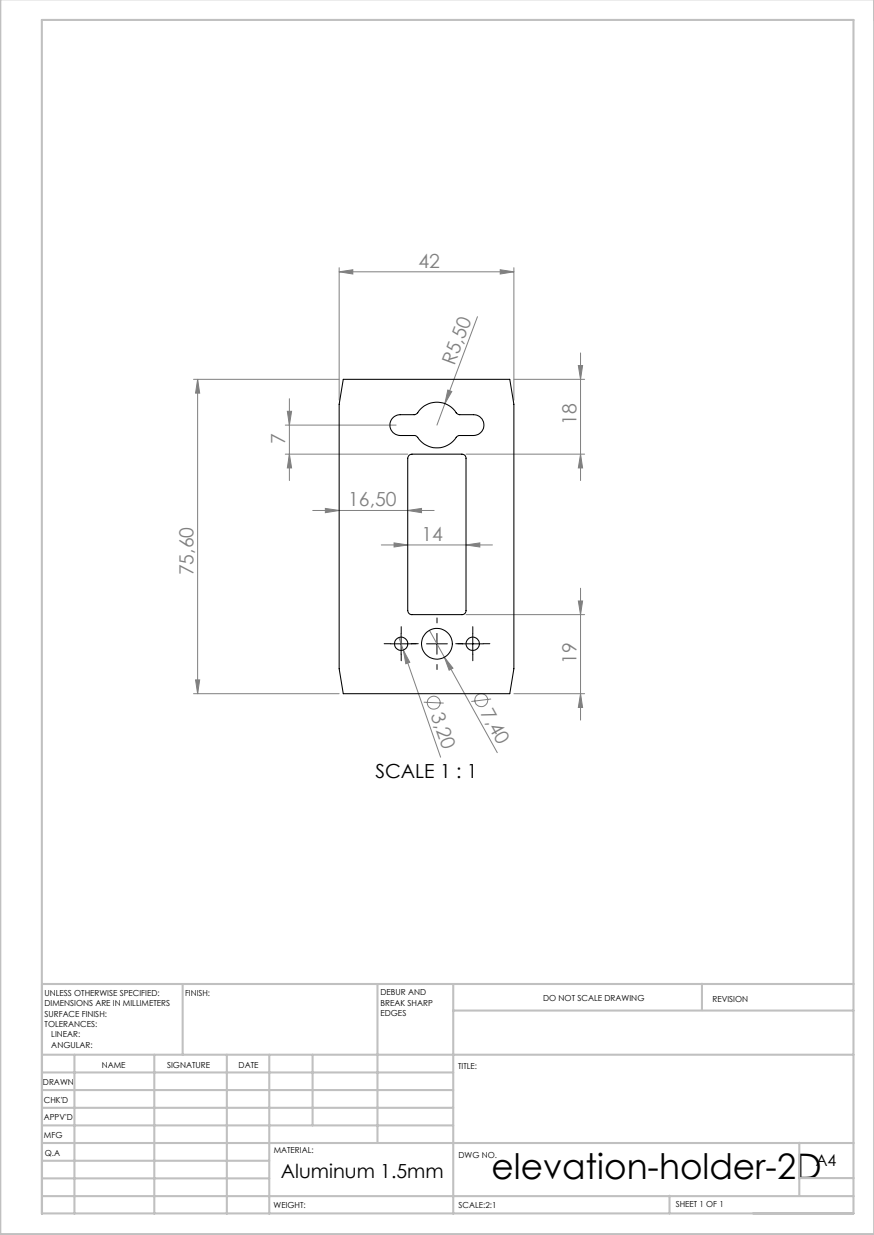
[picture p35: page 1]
SCALE 1 : 1; SCALE:2:1; SHEET 1 OF 1; DO NOT SCALE DRAWING; REVISION; DEBUR AND BREAK SHARP; UNLESS OTHERWISE SPECIFIED:; FINISH:

DIMENSIONS ARE IN MILLIMETERS
SURFACE FINISH:
TOLERANCES:
LINEAR:
ANGULAR:

NAME | SIGNATURE | DATE | | | | TITLE:
Q.A | | | | Aluminum 1.5mm MATERIAL: | elevation-holder-2D WEIGHT: DWG NO. | A4

DRAWN
CHK'D
APPV'D
MFG

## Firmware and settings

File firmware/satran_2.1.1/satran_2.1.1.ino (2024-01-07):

/********************************************
 * Satran Firmware MK2/3 v2.1.1
 * Daniel Nikolajsen 2022 <satran@danaco.se>
 * www.satran.io
 * Creative Commons BY-NC-SA 2.0
 *******************************************/

#include <ESP8266WiFi.h>
#include <WiFiClient.h>
#include <WiFiServer.h>
#include <ESP8266WebServer.h>
#include <EEPROM.h>

/* Fallback sensor min/max values */
int minAzValue = 200;
int maxAzValue = 700;
int minElValue = 350;
int maxElValue = 650;

/* Web and HTTP server */
ESP8266WebServer server(80);
IPAddress apIP(192, 168, 4, 1);
IPAddress netMsk(255, 255, 255, 0);
String ssid;
String pass;
String ssidList;
String hostName = "SATRAN_VhfSUghPX";

/* Hamlib/rotctl TCP server */
WiFiServer server2(4533);
WiFiClient client1;
String rotctl;

String page;
String page2;
String calibrationPage;
String versioncode = "SATRAN firmware 2.1.1<br/>&copy; 2022-10-19 Danaco";
String formvalues = "<script>(function() { var queries = new URLSearchParams(window.location.search); var az = document.getElementById('az'); var el = document.getElementById('el'); az.value = queries.get('az'); el.value = queries.get('el');})();</script>";
String favicon = "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";
String pageheader = "<!DOCTYPE html><html><head><title>SATRAN</title><meta name='viewport' content='width=device-width, initial-scale=1.0'><link rel='icon' href='" + favicon + "'><style>body{font-family:verdana,helvetica,sans-serif;padding:25px;}input,select{width:100%;max-width:350px;padding:6px 12px;margin-bottom:10px; box-sizing: border-box;}.btn{cursor:pointer;padding:10px;background:#eee;border:1px solid #777;border-radius:4px;margin:10px;min-width:200px;}#submit{margin:20px auto;}</style></head>";
String error;
int errorAz = 0;
int errorEl = 0;

int Pin_LED = 2;
int Pin_PWM = 15;
int Pin_Az1 = 12;
int Pin_Az2 = 14;
int Pin_SensAz = 5;
int Pin_El1 = 13;
int Pin_El2 = 0;
int Pin_SensEl = 4;

int readAz = 1;  // Measured sensor values
int readEl = 1;
int posAz = 1;  // Last (correct) position, used to prevent radio interference or sensor glitch
int posEl = 1;

int ResetState = 1;
int Pin_Reset = 16;

void setup(void) {

  Serial.begin(9600);
  EEPROM.begin(512);

  /* Initialize IOs */
  pinMode(Pin_Az1, OUTPUT);
  pinMode(Pin_Az2, OUTPUT);
  pinMode(Pin_El1, OUTPUT);
  pinMode(Pin_El2, OUTPUT);
  pinMode(Pin_PWM, OUTPUT);
  haltMotors();
  pinMode(Pin_LED, OUTPUT);
  digitalWrite(Pin_LED, HIGH); /* Turn off status LED. Reverse logic! */
  pinMode(Pin_SensAz, OUTPUT); /* Outputs that later are read by ADC pin */
  pinMode(Pin_SensEl, OUTPUT);
  digitalWrite(Pin_SensAz, LOW);
  digitalWrite(Pin_SensEl, LOW);

  readCalibration(); /* Update fallback values with stored sensor limits */
  posAz = readPosition("azimuth");
  posEl = readPosition("elevation");

  /* Scan available networks */
  int n = WiFi.scanNetworks();
  delay(50);
  ssidList = "<select id=\"newssid\" name=\"newssid\">";
  for (int i = 0; i < n; ++i) {
    ssidList += "<option value=\"";
    ssidList += WiFi.SSID(i);
    ssidList += "\">";
    ssidList += WiFi.SSID(i);
    ssidList += "</option>";
  }
  ssidList += "</select>";

  /* Setup WLAN */
  ssid = getWifiCredential("ssid");
  pass = getWifiCredential("pass");
  if (ssid != "n/a" && pass != "n/a") {
    if (!wifiConnect(ssid, pass)) {
      // create HOTSPOT if cant connect to Wifi
      WiFi.hostname(hostName);
      WiFi.mode(WIFI_AP);  // Enable AP
      WiFi.softAPConfig(apIP, apIP, netMsk);
      WiFi.softAP(hostName);  // Start AP
    }
  } else {
    // No Wifi credentials found, instead create HOTSPOT
    WiFi.hostname(hostName);
    WiFi.mode(WIFI_AP);  // Enable AP
    WiFi.softAPConfig(apIP, apIP, netMsk);
    WiFi.softAP(hostName);  // Start AP
  }

  /* Check that motors and sensors are working, then point north */
  initializeRotator();

  /* Server web page listeners */
  server.on("/", []() {
    int newAz = readPosition("azimuth");
    int newEl = readPosition("elevation");
    if (error == "") {
      page = pageheader + "<body style='text-align:center;'><h1>SATRAN Rotator</h1><p><form action='./manual' method='get'>Azimuth (1 - 360)<br/><input type='number' id='az' name='az' min='1' max='360' value=\"" + posAz + "\" placeholder=\"" + posAz + "\"><br/>Elevation (1 - 90)<br/><input type='number' id='el' name='el' min='1' max='90' value=\"" + posEl + "\" placeholder=\"" + posEl + "\"><br/><input type='submit' value='Execute'></form></p><p style='font-size:0.8em;color:#888;'>" + versioncode + "<br/>Current position: Azimuth " + newAz + " (memory " + posAz + ") / Elevation " + newEl + " (memory " + posEl + ") degrees<br/>Sensor values: Azimuth " + readAz + " / Elevation " + readEl + "</p>" + formvalues + "</body></html>";
    } else {
      page = pageheader + "<body style='text-align:center;'><h1>SATRAN Rotator</h1><p><strong>" + error + "</strong></p><p style='font-size:0.8em;color:#888;'>" + versioncode + "</p></body></html>";
    }
    server.send(200, "text/html", page);
  });

  server.on("/ping", []() {
    server.send(200, "text/html", "SATRAN");  //WiFi.localIP()
  });

  server.on("/manual", []() {
    // Receive coordinates via GET and turn the rotor
    int azimuth = server.arg("az").toInt();
    int elevation = server.arg("el").toInt();

    if (azimuth > 0 && elevation > 0) { turnMotors(azimuth, elevation); }

    int newAz = readPosition("azimuth");
    int newEl = readPosition("elevation");
    if (error == "") {
      page = pageheader + "<body style='text-align:center;'><h1>SATRAN Rotator</h1><p><form action='./manual' method='get'>Azimuth (1 - 360)<br/><input type='number' id='az' name='az' min='1' max='360' value=\"" + newAz + "\"><br/>Elevation (1 - 90)<br/><input type='number' id='el' name='el' min='1' max='90' value=\"" + newEl + "\"><br/><input type='submit' value='Execute'></form></p><p style='font-size:0.8em;color:#888;'>" + versioncode + "<br/>Current position: Azimuth " + newAz + " (memory " + posAz + ") / Elevation " + newEl + " (memory " + posEl + ") degrees<br/>Sensor values: Azimuth " + readAz + " / Elevation " + readEl + "</p>" + formvalues + "</body></html>";
    } else {
      page = pageheader + "<body style='text-align:center;'><h1>SATRAN Rotator</h1><p><strong>" + error + "</strong></p><p style='font-size:0.8em;color:#888;'>" + versioncode + "</p></body></html>";
    }
    server.send(200, "text/html", page);
  });

  server.on("/tracker", []() {
    if (error == "") {
      // Receive coordinates via GET and turn the rotor
      int azimuth = server.arg("az").toInt();
      int elevation = server.arg("el").toInt();

      if (azimuth > -1 && azimuth < 361 && elevation > -1 && elevation < 91) {
        turnMotors(azimuth, elevation);
      } else {
        server.send(200, "text/html", "Incorrect target values submitted (Azimuth 0-360, Elevation 0-90)");
      }

      server.send(200, "text/html", "success");
    } else {
      server.send(404, "text/html", "Error : " + error);
    }
  });


  // SETUP PAGE
  page2 = pageheader + "<body style='text-align:center;'><em>Saving and restarting. Please connect your device back to your wifi.</em></body></html>";

  server.on("/setup", []() {
    page = pageheader + "<body style='text-align:center;'><h1>SATRAN Rotator - WLAN Setup</h1><p>" + error + "</p><p><form action='/savesettings' method='get'>Network<br/>" + ssidList + "<br/><br/>Password<br/><input type='text' id='newpass' name='newpass'><br/><br/><input type='submit' id='submit' value='Save'></form>";
    page += "</p><p style='font-size:0.8em;color:#888;'>Can't find your access point?<br/> SATRAN only supports b/g/n-type networks.<br/><br/>" + versioncode + "</p></body></html>";

    server.send(200, "text/html", page);
  });
  server.on("/savesettings", []() {
    //Saving Wifi Credentials

    // Clean inputs
    String newSsid = server.arg("newssid");
    newSsid.trim();
    String newPass = server.arg("newpass");
    newPass.trim();

    if (saveWifiCredentials(newSsid, newPass)) {
      //Saving and restarting
      server.send(200, "text/html", page2);
      delay(3000);
    } else {
      error = "Could not save wifi credentials. Restarting unit.";
    }
    ESP.restart();
  });

  server.on("/calibration", []() {
    readAz = readSensor("azimuth");
    readEl = readSensor("elevation");
    calibrationPage = pageheader + "<body style='text-align:center;'><script>function rotate(command){ fetch('./microstep?action='+command).then(data => { console.log(data); location.reload(); }); }</script>";
    calibrationPage = calibrationPage + error + "<h1>SATRAN Calibration</h1>";
    calibrationPage = calibrationPage + "<button type='button' onclick='rotate(\"ccw\");' class='btn'>Azimuth CCW</button> <input type='text' value='" + readAz + "' readonly style='width:70px;'> <button type='button' onclick='rotate(\"cw\");' class='btn'>Azimuth CW</button><br><button type='button' onclick='rotate(\"down\");' class='btn'>Elevation Down</button> <input type='text' value='" + readEl + "' readonly style='width:70px;'> <button type='button' onclick='rotate(\"up\");' class='btn'>Elevation Up</button><br><br>";
    calibrationPage = calibrationPage + "<FORM action='/storecalibration' method='get'>Azimuth min (0 degrees north): <input type='text' id='minAz' name='minAz' value='" + minAzValue + "' style='width:80px;'><br>Azimuth max (360 degrees north): <input type='text' id='maxAz' name='maxAz' value='" + maxAzValue + "' style='width:80px;'><br>Elevation min (0 degrees, horizontal): <input type='text' id='minEl' name='minEl' value='" + minElValue + "' style='width:80px;'><br>Elevation max (90 degrees, vertical): <input type='text' id='maxEl' name='maxEl' value='" + maxElValue + "' style='width:80px;'><br><input type='submit' id='submit' value='Save calibration'></FORM></body></html>";
    error = ""; /* Reset any messages already sent to browser */
    server.send(200, "text/html", calibrationPage);
  });

  server.on("/microstep", []() {
    if (error == "") {
      // Receive coordinates via GET and turn the rotor
      String command = server.arg("action");
      analogWrite(Pin_PWM, 255);
      delay(10);
      if (command == "cw") {
        digitalWrite(Pin_Az1, HIGH);
        delay(20);
        haltMotors();
        delay(200);
        int readAz = readSensor("azimuth"); /* Read the new values */
      } else if (command == "ccw") {
        digitalWrite(Pin_Az2, HIGH);
        delay(20);
        haltMotors();
        delay(200);
        int readAz = readSensor("azimuth"); /* Read the new values */
      } else if (command == "down") {
        digitalWrite(Pin_El1, HIGH);
        delay(20);
        haltMotors();
        delay(200);
        int readEl = readSensor("elevation");
      } else if (command == "up") {
        digitalWrite(Pin_El2, HIGH);
        delay(20);
        haltMotors();
        delay(200);
        int readEl = readSensor("elevation");
      }

      calibrationPage = pageheader + "<body style='text-align:center;'><script>function rotate(command){ fetch('./manual?action='+command).then(data => { console.log(data); location.reload(); }); }</script>";
      calibrationPage = calibrationPage + error + "<h1>SATRAN Calibration</h1>";
      calibrationPage = calibrationPage + "<button type='button' onclick='rotate(\"ccw\");' class='btn'>Azimuth CCW</button> <input type='text' value='" + readAz + "' readonly style='width:70px;'> <button type='button' onclick='rotate(\"cw\");' class='btn'>Azimuth CW</button><br><button type='button' onclick='rotate(\"down\");' class='btn'>Elevation Down</button> <input type='text' value='" + readEl + "' readonly style='width:70px;'> <button type='button' onclick='rotate(\"up\");' class='btn'>Elevation Up</button><br><br>";
      calibrationPage = calibrationPage + "<FORM action='/storecalibration' method='get'>Azimuth min (0 degrees north): <input type='text' id='minAz' name='minAz' value='" + minAzValue + "' style='width:80px;'><br>Azimuth max (360 degrees north): <input type='text' id='maxAz' name='maxAz' value='" + maxAzValue + "' style='width:80px;'><br>Elevation min (0 degrees, horizontal): <input type='text' id='minEl' name='minEl' value='" + minElValue + "' style='width:80px;'><br>Elevation max (90 degrees, vertical): <input type='text' id='maxEl' name='maxEl' value='" + maxElValue + "' style='width:80px;'><br><input type='submit' id='submit' value='Save calibration'></FORM></body></html>";

      server.send(200, "text/html", "success");
    } else {
      server.send(200, "text/html", "error");
    }
  });

  server.on("/storecalibration", []() {
    String MinAz = server.arg("minAz");
    String MaxAz = server.arg("maxAz");
    String MinEl = server.arg("minEl");
    String MaxEl = server.arg("maxEl");

    if (saveCalibration(MinAz, MaxAz, MinEl, MaxEl)) {
      error = "Settings saved!";
    } else {
      error = "Error! Could not save calibration values.";
    }
    server.send(200, "text/html", "<head><meta http-equiv=\"refresh\" content=\"0;url=./calibration\"></head>");
  });

  server.begin();
  server2.begin();

}  // End setup


/***************************************
 * Here comes all the various functions
 ***************************************/


bool wifiConnect(String ssid, String pass) {
  /* Connect to a Wifi network and returns true or false */
  if (ssid.length() > 0 && pass.length() > 0) {
    /* Explicitly set the ESP8266 to be a WiFi-client, otherwise, it by default,
     would try to act as both a client and an access-point and could cause
     network-issues with your other WiFi-devices on your WiFi-network. */
    WiFi.mode(WIFI_STA);
    WiFi.hostname(hostName);  // Custom wifi device name, set in header
    WiFi.begin(ssid, pass);   //begin WiFi connection

    // Wait for connection
    int conn_count = 0;
    while (WiFi.status() != WL_CONNECTED && conn_count < 30) {
      delay(1000);
      conn_count++;
    }
    if (WiFi.status() == WL_CONNECTED) {
      //Serial.println(WiFi.localIP());
      return true;
    } else {
      return false;
    }
  } else {
    return false;
  }
}


bool saveWifiCredentials(String ssid, String pass) {

  if (ssid.length() == 0 || pass.length() == 0) { return false; }

  // Clear EEPROM memory first
  for (int i = 0; i < 64; ++i) {
    EEPROM.write(i, 0);
  }

  // Save SSID
  if (ssid.length() < 10) {
    EEPROM.write(0, 0);
    EEPROM.write(1, ssid.length());
  } else {
    int firstchar = 0;
    int lastchar = 0;
    if (ssid.length() > 20) {
      /* 20-29 */
      firstchar = 2;
      lastchar = ssid.length() - 20;
    } else {
      /* 10-19 */
      firstchar = 1;
      lastchar = ssid.length() - 10;
    }
    EEPROM.write(0, firstchar);
    EEPROM.write(1, lastchar);
  }
  for (int i = 2; i < ssid.length() + 2; ++i) {
    int n = i - 2;
    EEPROM.write(i, ssid[n]);
  }

  // Save password
  if (pass.length() < 10) {
    EEPROM.write(32, 0);
    EEPROM.write(33, pass.length());
  } else {
    int firstchar = 0;
    int lastchar = 0;
    if (pass.length() > 19) {
      /* 20-29 */
      firstchar = 2;
      lastchar = pass.length() - 20;
    } else {
      /* 10-19 */
      firstchar = 1;
      lastchar = pass.length() - 10;
    }
    EEPROM.write(32, firstchar);
    EEPROM.write(33, lastchar);
  }
  for (int i = 34; i < pass.length() + 34; ++i) {
    int n = i - 34;
    EEPROM.write(i, pass[n]);
  }
  EEPROM.commit();

  return true;
}


String getWifiCredential(String value) { /* Fetch wifi login details stored in memory */
  if (value == "ssid") {
    if (EEPROM.read(0) + EEPROM.read(1) > 0) {
      //Reading saved wifi credentials
      // First two bytes contains length of string
      int len = char(EEPROM.read(0)) * 10 + char(EEPROM.read(1));
      len = len + 2;
      for (int i = 2; i < len; ++i) {
        ssid += char(EEPROM.read(i));
      }
      return ssid;
    } else {
      return "n/a";
    }

  } else if (value == "pass") {
    if (EEPROM.read(32) + EEPROM.read(33) > 0) {
      int len = char(EEPROM.read(32)) * 10 + char(EEPROM.read(33));
      len = len + 34;
      for (int i = 34; i < len; ++i) {
        pass += char(EEPROM.read(i));
      }
      return pass;
    } else {
      return "n/a";
    }
  }
  return "n/a";
}


bool saveCalibration(String MinAz, String MaxAz, String MinEl, String MaxEl) {
  /* Clear EEPROM memory first */
  for (int i = 64; i < 76; ++i) {
    EEPROM.write(i, 0);
  }

  /* TODO check for length of variables to fit inside max/min */
  if (MinAz.length() == 1) { MinAz = "00" + MinAz; }
  if (MinAz.length() == 2) { MinAz = "0" + MinAz; }
  if (MaxAz.length() == 1) { MaxAz = "00" + MaxAz; }
  if (MaxAz.length() == 2) { MaxAz = "0" + MaxAz; }
  if (MinEl.length() == 1) { MinEl = "00" + MinEl; }
  if (MinEl.length() == 2) { MinEl = "0" + MinEl; }
  if (MaxEl.length() == 1) { MaxEl = "00" + MaxEl; }
  if (MaxEl.length() == 2) { MaxEl = "0" + MaxEl; }

  if (MinAz.length() == 3) {
    EEPROM.write(64, char(MinAz[0]));
    EEPROM.write(65, char(MinAz[1]));
    EEPROM.write(66, char(MinAz[2]));
  } else {
    return false;
  }
  if (MaxAz.length() == 3) {
    EEPROM.write(67, MaxAz[0]);
    EEPROM.write(68, MaxAz[1]);
    EEPROM.write(69, MaxAz[2]);
  } else {
    return false;
  }
  if (MinEl.length() == 3) {
    EEPROM.write(70, MinEl[0]);
    EEPROM.write(71, MinEl[1]);
    EEPROM.write(72, MinEl[2]);
  } else {
    return false;
  }
  if (MaxEl.length() == 3) {
    EEPROM.write(73, MaxEl[0]);
    EEPROM.write(74, MaxEl[1]);
    EEPROM.write(75, MaxEl[2]);
  } else {
    return false;
  }

  EEPROM.commit();
  delay(10);
  minAzValue = MinAz.toInt();
  maxAzValue = MaxAz.toInt();
  minElValue = MinEl.toInt();
  maxElValue = MaxEl.toInt();

  return true;
}

void readCalibration(void) {
  String value = (String) char(EEPROM.read(64)) + char(EEPROM.read(65)) + char(EEPROM.read(66));
  if (value.toInt() > 30 && value.toInt() < 1000) { minAzValue = value.toInt(); }

  value = (String) char(EEPROM.read(67)) + char(EEPROM.read(68)) + char(EEPROM.read(69));
  if (value.toInt() > 30 && value.toInt() < 1000) { maxAzValue = value.toInt(); }

  value = (String) char(EEPROM.read(70)) + char(EEPROM.read(71)) + char(EEPROM.read(72));
  if (value.toInt() > 30 && value.toInt() < 1000) { minElValue = value.toInt(); }

  value = (String) char(EEPROM.read(73)) + char(EEPROM.read(74)) + char(EEPROM.read(75));
  if (value.toInt() > 30 && value.toInt() < 1000) { maxElValue = value.toInt(); }
}
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
void loop(void) {
  server.handleClient();
  readResetButton();

  /* Hamlib/rotctl TCP socket */
  client1 = server2.available();
  while (client1 && client1.connected()) {
    rotctl = client1.readStringUntil('\n');
    Serial.println(rotctl);
    if (char(rotctl[0]) == 'p' || rotctl.indexOf("get_pos") > 0) {
      int azPos = readPosition("azimuth");
      int elPos = readPosition("elevation");
      if (azPos > -1 && azPos < 361 && elPos > -1 && elPos < 91) {
        client1.print(String(azPos) + ".0\n" + String(elPos) + ".0\n");
      } else {
        client1.print("RPRT -6\n");
      }
    }
    if (char(rotctl[0]) == 'P' || rotctl.indexOf("set_pos") > 0) {
      int divider;
      if (char(rotctl[0]) == 'P') {
        divider = 2;
      } else {
        divider = 8;
      }
      String part1 = rotctl.substring(divider, rotctl.indexOf(" ", divider));
      String part2 = rotctl.substring(rotctl.indexOf(" ", divider), rotctl.length());
      int newAz = part1.toInt();
      int newEl = part2.toInt();
      if (newAz > -1 && newAz < 361 && newEl > -1 && newEl < 91) {
        turnMotors(newAz, newEl);
        client1.print("RPRT 0\n");
      } else {
        client1.print("RPRT -6\n");
      }
    }
    if (char(rotctl[0]) == 'M' || rotctl.indexOf("move") > 0) { client1.print("RPRT -4\n"); /* command not supported by satran */ }
    if (char(rotctl[0]) == 'C' || rotctl.indexOf("set_conf") > 0) { client1.print("RPRT -4\n"); /* command not supported by satran */ }
    if (char(rotctl[0]) == 'S' || rotctl.indexOf("stop") > 0) { /* Stop */
      haltMotors();
      client1.print("RPRT 0\n");
    }
    if (char(rotctl[0]) == 'K' || rotctl.indexOf("park") > 0) { /* Park */
      initializeRotator();
      client1.print("RPRT 0\n");
    }
    if (char(rotctl[0]) == '_' || rotctl.indexOf("get_info") > 0) { client1.print("Info SATRAN v.2.1.1 az/el rotator\n"); }
    if (char(rotctl[0]) == 'R' || rotctl.indexOf("reset") > 0) {
      client1.stop();
      ESP.restart();
    }
    rotctl = "";
    delay(200);
  }
  client1.stop();
}

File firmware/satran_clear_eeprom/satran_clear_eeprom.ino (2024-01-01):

/********************************************
 * Satran ESP8266 EEPROM-wiper
 * Daniel Nikolajsen 2022 <satran@danaco.se>
 * www.satran.io
 * Creative Commons BY-NC-SA 2.0
 *******************************************/
 
 #include <EEPROM.h>

void setup() {
  // USED TO CLEAR THE EEPROM BEFORE FIRST FIRMWARE UPLOAD
  Serial.begin(9600); 
  EEPROM.begin(512);
  delay(100);
  for (int i = 0; i < 120; ++i) {
    EEPROM.write(i, 0);
  }
  EEPROM.commit(); 
    delay(500);
  Serial.println("Memory cleared");

}

void loop() {

}

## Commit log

2024-01-01 Rename files and unpack 3D print files
    [antenna-bracket-15mm.STL, antenna-bracket-20mm.STL, axle-spacer.STL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]
2024-01-01 Add K0SWE's sheet metal dxf files
    [Antenna bracket flat.dxf, Elevation motor bracket flat.dxf]
2024-01-01 Add link to K0SWE's BOM
2024-01-01 Update patchboard schematic
    Fix swapped Az and El wire colors. Add cable assemblies. Maybe it should have been obvious, but the old one was not obvious to me.
2024-01-01 Add onshape URL
    And newline at the end of BOM url.
2024-01-07 Use Arduino IDE auto format
2024-01-07 Fix warning about return type
    [satran_2.1.1.ino]
